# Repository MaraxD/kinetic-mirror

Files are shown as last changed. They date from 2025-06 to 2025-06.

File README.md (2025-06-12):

# Kinetic mirror - an interactive installation

## Materials used
<ul>
<li>
    32 Micro Servomotor SG90 90°
</li>
<li>
    Arduino Uno board
</li>
<li>
    32 mirror panels
</li>
<li>
    2 PCA PWM boards
</li>
<li>
    2 external power sources
</li>
</ul>

## Prerequisites
1. Clone this repository and make you have Arduino and Max installed
2. Clone this MediaPipe bundle for Max, https://github.com/lysdexic-audio/jweb-hands-landmarker. 
3. After cloning, drag and drop the dataprocessing file into the jweb-hands-landmarker folder. Double tap on the [dataprocessing] component to check if it was corectly added.

4. Install the Servo library and the Adafruit PWM Servo Driver library

## Wiring up Arduino Uno to the first PWM boards
Arduino | PWM board 1 | Info | 
--- | --- | --- 
GND | GND | Ground 
A5 | SCL | Serial Clock 
A4 | SDA | Serial Data 
5V | VCC | Power

## Wiring up the two PWM boards
PWM board 1 | PWM board 2 | Info | 
--- | --- | --- 
GND | GND | Ground 
OE | OE | Output Enable
SCL | SCL | Serial Clock 
SDA | SDA | Serial Data
VCC | VCC | Power
V+ | V+ | Power

<b>!!</b> both PWM board share the same address (0x40), in order to differentiate between the two of them change the address to 0x41 on the second one by souldering a bridge across the first terminals on the right, just like in the picture below:

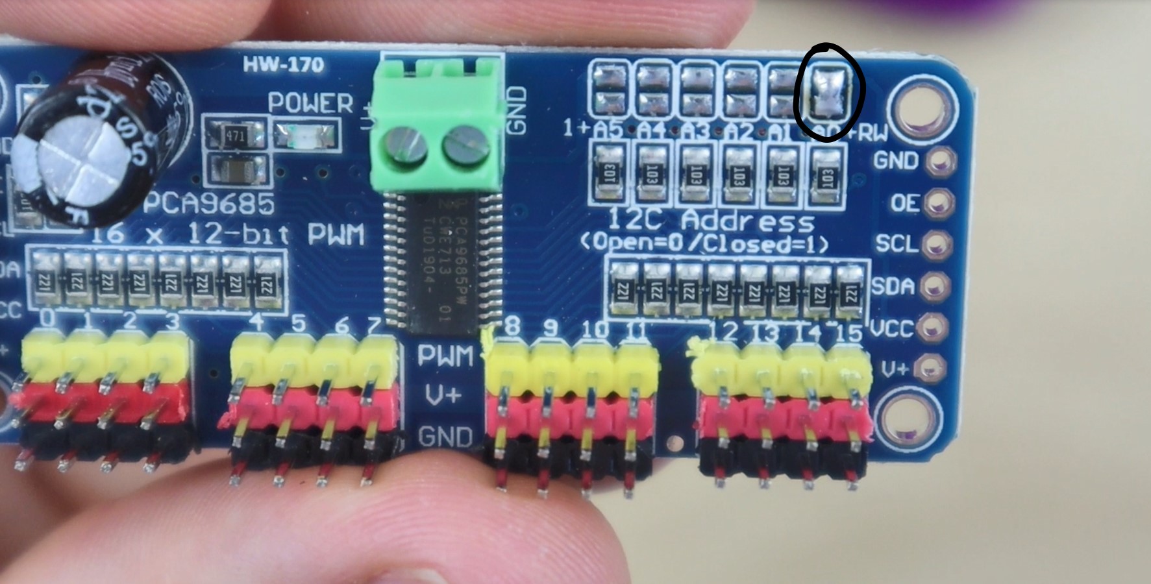
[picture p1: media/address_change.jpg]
 

## Wiring up the motors and the external power source to the PWM boards
The wires on the motors are pretty self explenatory and resemble the colors on the board, the brown wire goes to ground and the orange wire is the PWM signal.
For powering up the servo motors I recommend using a 5V power supply (no higher than 6V) with a minimum of 9-10A (depending on the number of servo motors and how frequent you want to move them). Below is a simple calculation (thanks to https://github.com/aaronse/servo-display/discussions/11), to get an idea of how much 16 motors consume:<br>
~10ma * 16 servos = 160ma when idle (common scenario)<br>
~250ma * 16 servos = 4A if continuous motion (rare scenario. Expect subset of 16 servos moving, and slow movements at any given time).<br>
~750ma * 16 servos = 12A if all fully stalled (Should never happen, but… Code Bugs… So will happen when software has bug(s)).<br>

In my case, I used two power supplies (not really recommended), each attached to its own PWM board. The red wire goes into the left inlet while the other wire goes into the other input.

If you want to see the full detailed diagram, check diagram.fzz.

## Demo
Plug in the Arduino board and the power supplies, load the script (from the motors_script folder) and open the Max patch (jweb-hands-landmarker/jweb-hands-landmarker.maxpat). <br>
<b>!!! When opening up the patch you will see a [serial c 115200] component, press on print to see all the available ports and modify the letter in the component corresponding to the port that Arduino is using (so in my case c: usbm_modem xxx was the port Arduino was communicating on). !!!<br>
!!! If you choose to change the baud rate, make sure you also change it in the Max patch !!!</b>



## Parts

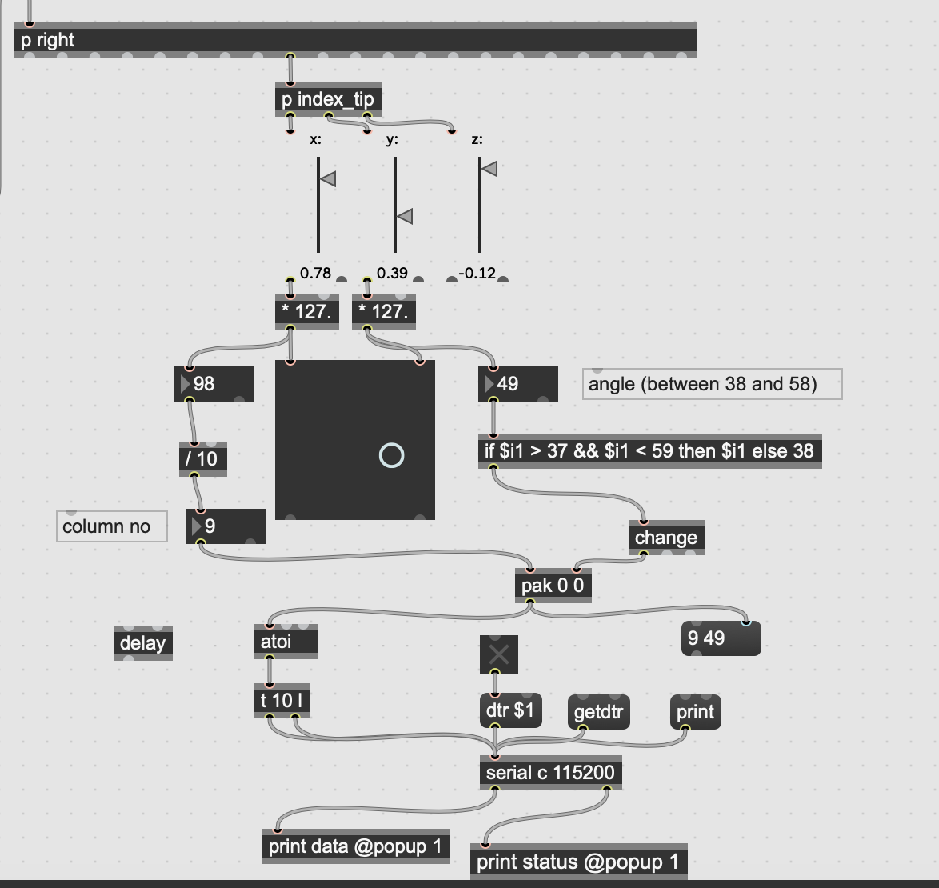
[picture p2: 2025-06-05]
media/max_components.png

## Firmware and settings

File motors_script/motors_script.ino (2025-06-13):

/* Sweep
 by BARRAGAN <http://barraganstudio.com>
 This example code is in the public domain.

 modified 8 Nov 2013
 by Scott Fitzgerald
 http://www.arduino.cc/en/Tutorial/Sweep
*/

#include <Servo.h>                    //install Servo library
#include <Adafruit_PWMServoDriver.h>  // adafruit pwm servo driver library
#include <Thread.h>
#include <ThreadController.h>

Adafruit_PWMServoDriver board1 = Adafruit_PWMServoDriver(0x40);  // called this way, it uses the default address 0x40
Adafruit_PWMServoDriver board2 = Adafruit_PWMServoDriver(0x41);

ThreadController controller = ThreadController();

Thread animationThread = Thread();
Thread serialThread = Thread();

#define SERVOMIN 125  // this is the 'minimum' pulse length count (out of 4096)
#define SERVOMAX 625  // this is the 'maximum' pulse length count (out of 4096)


int colNumber, angle, time;
bool handDetected = false;
int startingColumnNo;

const int numColumns = 3;
int currentAngle[numColumns] = { 38 };
bool goingUp[numColumns] = { true };

unsigned long lastReceivedTime = 0;
const unsigned long handTimeout = 500;
unsigned long lastHandTime = 0;



void setup() {
  Serial.begin(115200);
  // Serial.println("16 channel Servo test!");

  board1.begin();
  board1.setOscillatorFrequency(27000000);  //Set the PWM oscillator frequency, used for fine calibration
  board1.setPWMFreq(50);

  board2.begin();
  board2.setOscillatorFrequency(27000000);
  board2.setPWMFreq(50);

  resetPanels();

  randomSeed(3);

  animationThread.onRun([]() {
    if (!handDetected) {
      delay(100);
      startingColumnNo = random(0, 6);
      secondIdleMode();
      resetPanels();
      idleMode();
      resetPanels();
      delay(100);
    }
  });
  animationThread.setInterval(50);

  serialThread.onRun([]() {
    if (Serial.available()) {

      colNumber = Serial.parseInt();
      angle = Serial.parseInt();

      if (Serial.read() == '\n') {
        handDetected = true;
        lastHandTime = millis();

        if (colNumber < 4) {

          board1.setPWM(4 * colNumber, 0, angleToPulse(angle));
          board1.setPWM(4 * colNumber + 1, 0, angleToPulse(angle));
          board1.setPWM(4 * colNumber + 2, 0, angleToPulse(angle));
          board1.setPWM(4 * colNumber + 3, 0, angleToPulse(angle));
        } else {

          //the rest of the logic will be on the second board
          board2.setPWM(((colNumber - 4) * 4) + 0, 0, angleToPulse(angle));
          board2.setPWM(((colNumber - 4) * 4) + 1, 0, angleToPulse(angle));
          board2.setPWM(((colNumber - 4) * 4) + 2, 0, angleToPulse(angle));
          board2.setPWM(((colNumber - 4) * 4) + 3, 0, angleToPulse(angle));
        }
      }
    }
  });
  serialThread.setInterval(10);

  controller.add(&animationThread);
  controller.add(&serialThread);
}

void loop() {

  controller.run();

  if (handDetected && millis() - lastHandTime > 3000) {
    handDetected = false;
  }




  //   if (handDetected) {
  //     handDetected = false;
  //     delay(100);
  //     startingColumnNo = random(0, 6);
  //     secondIdleMode();
  //     resetPanels();
  //     idleMode();
  //     resetPanels();
  //     delay(100);
  //   }
  // }
  // else {
  //   if (!handDetected) {
  //     handDetected = true;
  //   }
  // }
}

void resetPanels() {
  for (int i = 0; i < 16; i++) {
    board1.setPWM(i, 0, angleToPulse(45));
    board2.setPWM(i, 0, angleToPulse(45));
  }
}

int angleToPulse(int ang)  //gets angle in degree and returns the pulse width
{
  int pulse = map(ang, 0, 90, SERVOMIN, SERVOMAX);  // map angle of 0 to 90 to Servo min and Servo max
  Serial.write(pulse);
  return pulse;
}

void writeToColumn(int group, int angle) {
  int baseIndex = group * 4;
  int pulse = angleToPulse(angle);

  for (int i = 0; i < 4; i++) {
    int channel = baseIndex + i;
    if (channel < 16) {
      board1.setPWM(channel, 0, pulse);
    } else {
      board2.setPWM(channel - 16, 0, pulse);
    }
  }
}

void secondIdleMode() {
  for (int step = 0; step < 200; step++) {
    if (handDetected) return;
    for (int col = startingColumnNo; col < startingColumnNo + 3; col++) {
      int idx = col - startingColumnNo;
      if (step >= col * 10) {
        if (goingUp[idx]) {
          currentAngle[idx]++;
          if (currentAngle[idx] >= 58) goingUp[idx] = false;
        } else {
          currentAngle[idx]--;
          if (currentAngle[idx] <= 38) goingUp[idx] = true;
        }

        writeToColumn(col, currentAngle[idx]);
      }
    }
    delay(30);
  }
}

void idleMode() {
  for (int group = 0; group < 8; group++) {
    if (handDetected) return;
    int baseIndex = group * 4;
    bool isEven = group % 2 == 0;

    if (isEven) {
      for (int angle = 38; angle <= 58; angle += 5) {
        writeToColumn(group, angle);
        delay(50);
      }
    } else {
      for (int angle = 58; angle >= 38; angle -= 5) {
        writeToColumn(group, angle);
        delay(50);
      }
    }

    delay(200);
  }

  delay(500);
}
